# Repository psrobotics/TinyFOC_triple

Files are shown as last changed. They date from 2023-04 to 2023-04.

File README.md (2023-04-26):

# TinyFOC_triple

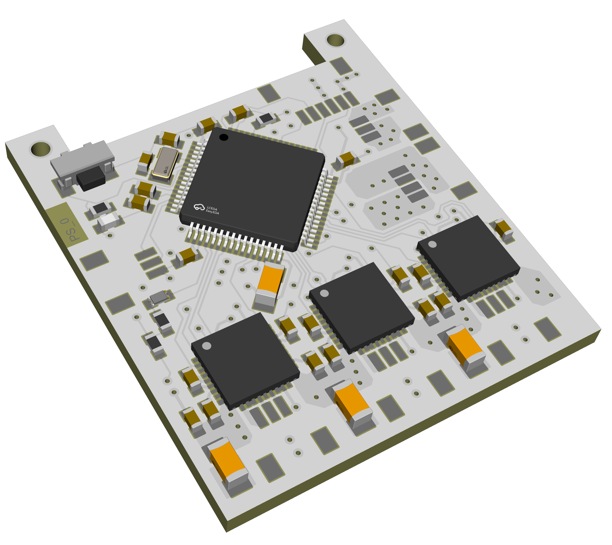
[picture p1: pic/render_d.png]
<br> <br>
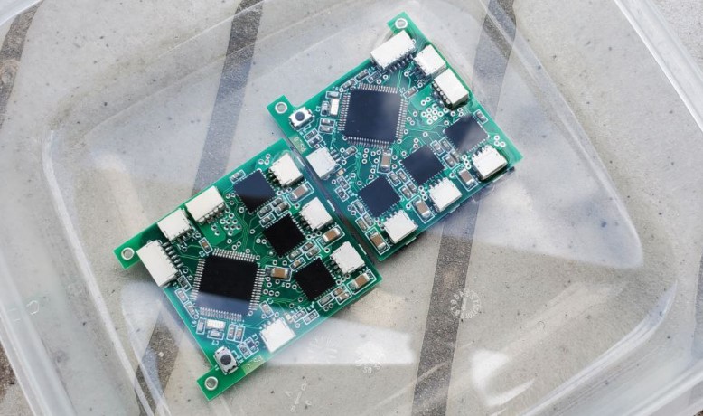
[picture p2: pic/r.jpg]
<br> <br>

* Compact 3 channel brushless motor driver with external encoder
* Supports I2C (AS5600) or AB (TLE5012B) encoders
* Hardwarer CAN, serial, SPI interface
* Input voltage: 9v - 24v, maximum phase current 1.5A
* 4 layer board / FR4 / 1.0mm thickness
* [SimpleFOC](https://github.com/simplefoc) compatible

Design file exported with [Autodesk EAGLE](https://www.autodesk.com/products/eagle/overview?term=1-YEAR&tab=subscription)

## ICs
* MCU [STM32F446RET6](https://www.st.com/en/microcontrollers-microprocessors/stm32f446re.html)
* Motor driver [DRV8313](https://www.ti.com/product/DRV8313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) or [MS8313](https://www.lcsc.com/product-detail/Others_Hangzhou-Ruimeng-Tech-MS8313_C231942.html)
* Encoder [AS5600](https://ams.com/en/as5600) or [TLE5012B E1000](https://www.infineon.com/cms/en/product/sensor/magnetic-sensors/magnetic-position-sensors/angle-sensors/tle5012b-e1000/)

## Pin Out
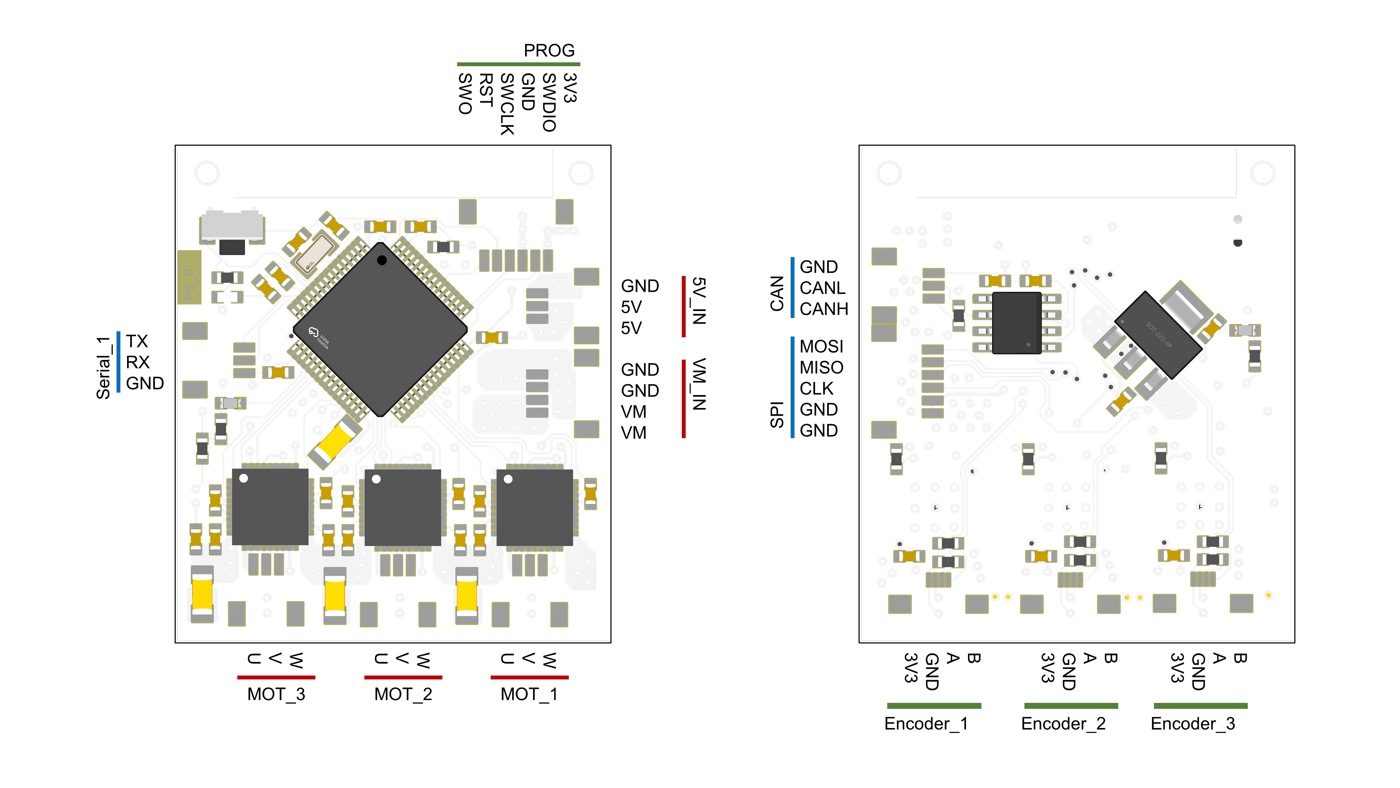
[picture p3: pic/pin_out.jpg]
<br> <br>

## License
MIT License

## Contact
* Shuang Peng, {shuangpe}@usc.edu

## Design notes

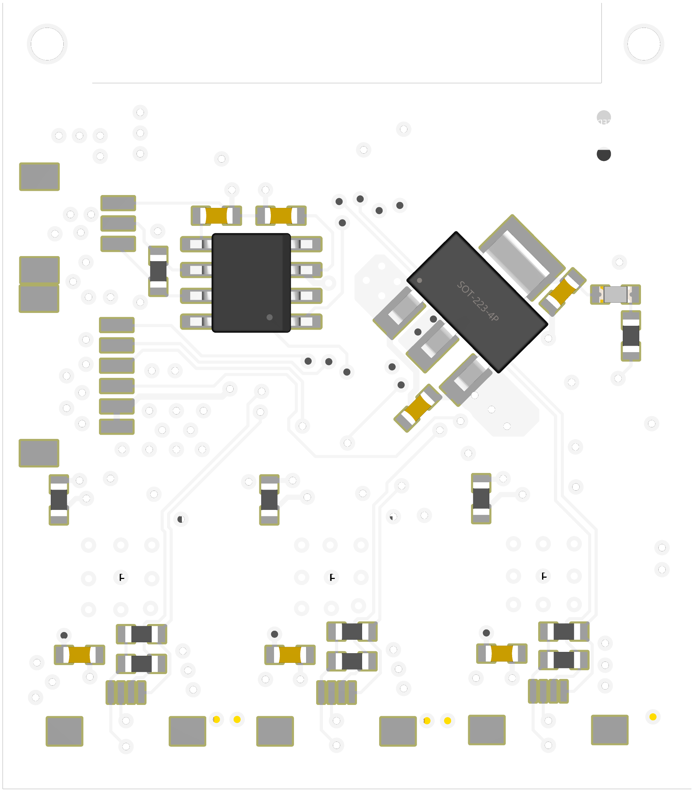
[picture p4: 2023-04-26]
pic/render_b.png

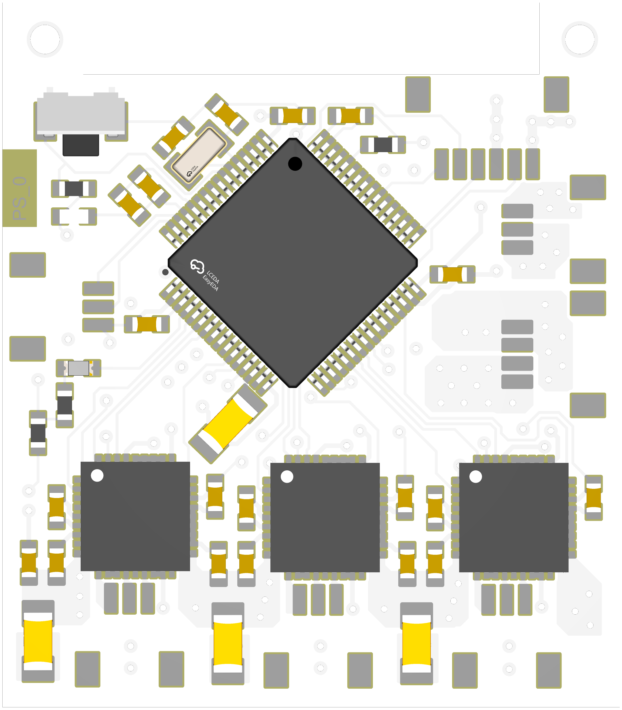
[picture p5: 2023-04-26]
pic/render_t.png

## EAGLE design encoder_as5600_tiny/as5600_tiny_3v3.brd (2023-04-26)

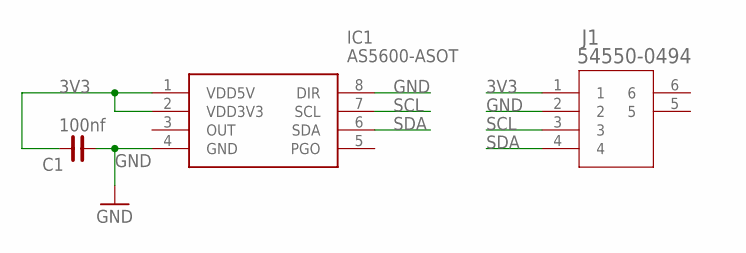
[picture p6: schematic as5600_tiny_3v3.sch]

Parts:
C1: 100nf; C0603
IC1: AS5600-ASOT; SOIC127P600X175-8N
J1: 54550-0494; CON4_1X4_DRB2_MOL

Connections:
3V3: C1.2, IC1.1 (VDD5V), IC1.2 (VDD3V3), J1.1
GND: C1.1, IC1.4 (GND), IC1.8 (DIR), J1.2
SCL: IC1.7 (SCL), J1.3
SDA: IC1.6 (SDA), J1.4

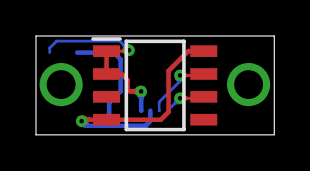
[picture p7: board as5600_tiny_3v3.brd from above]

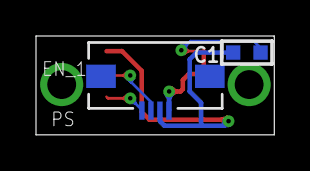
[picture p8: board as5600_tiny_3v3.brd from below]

Board: 2 copper layers, 13.2 x 5.5 mm, 3 parts (2 on the bottom side), 4 nets.

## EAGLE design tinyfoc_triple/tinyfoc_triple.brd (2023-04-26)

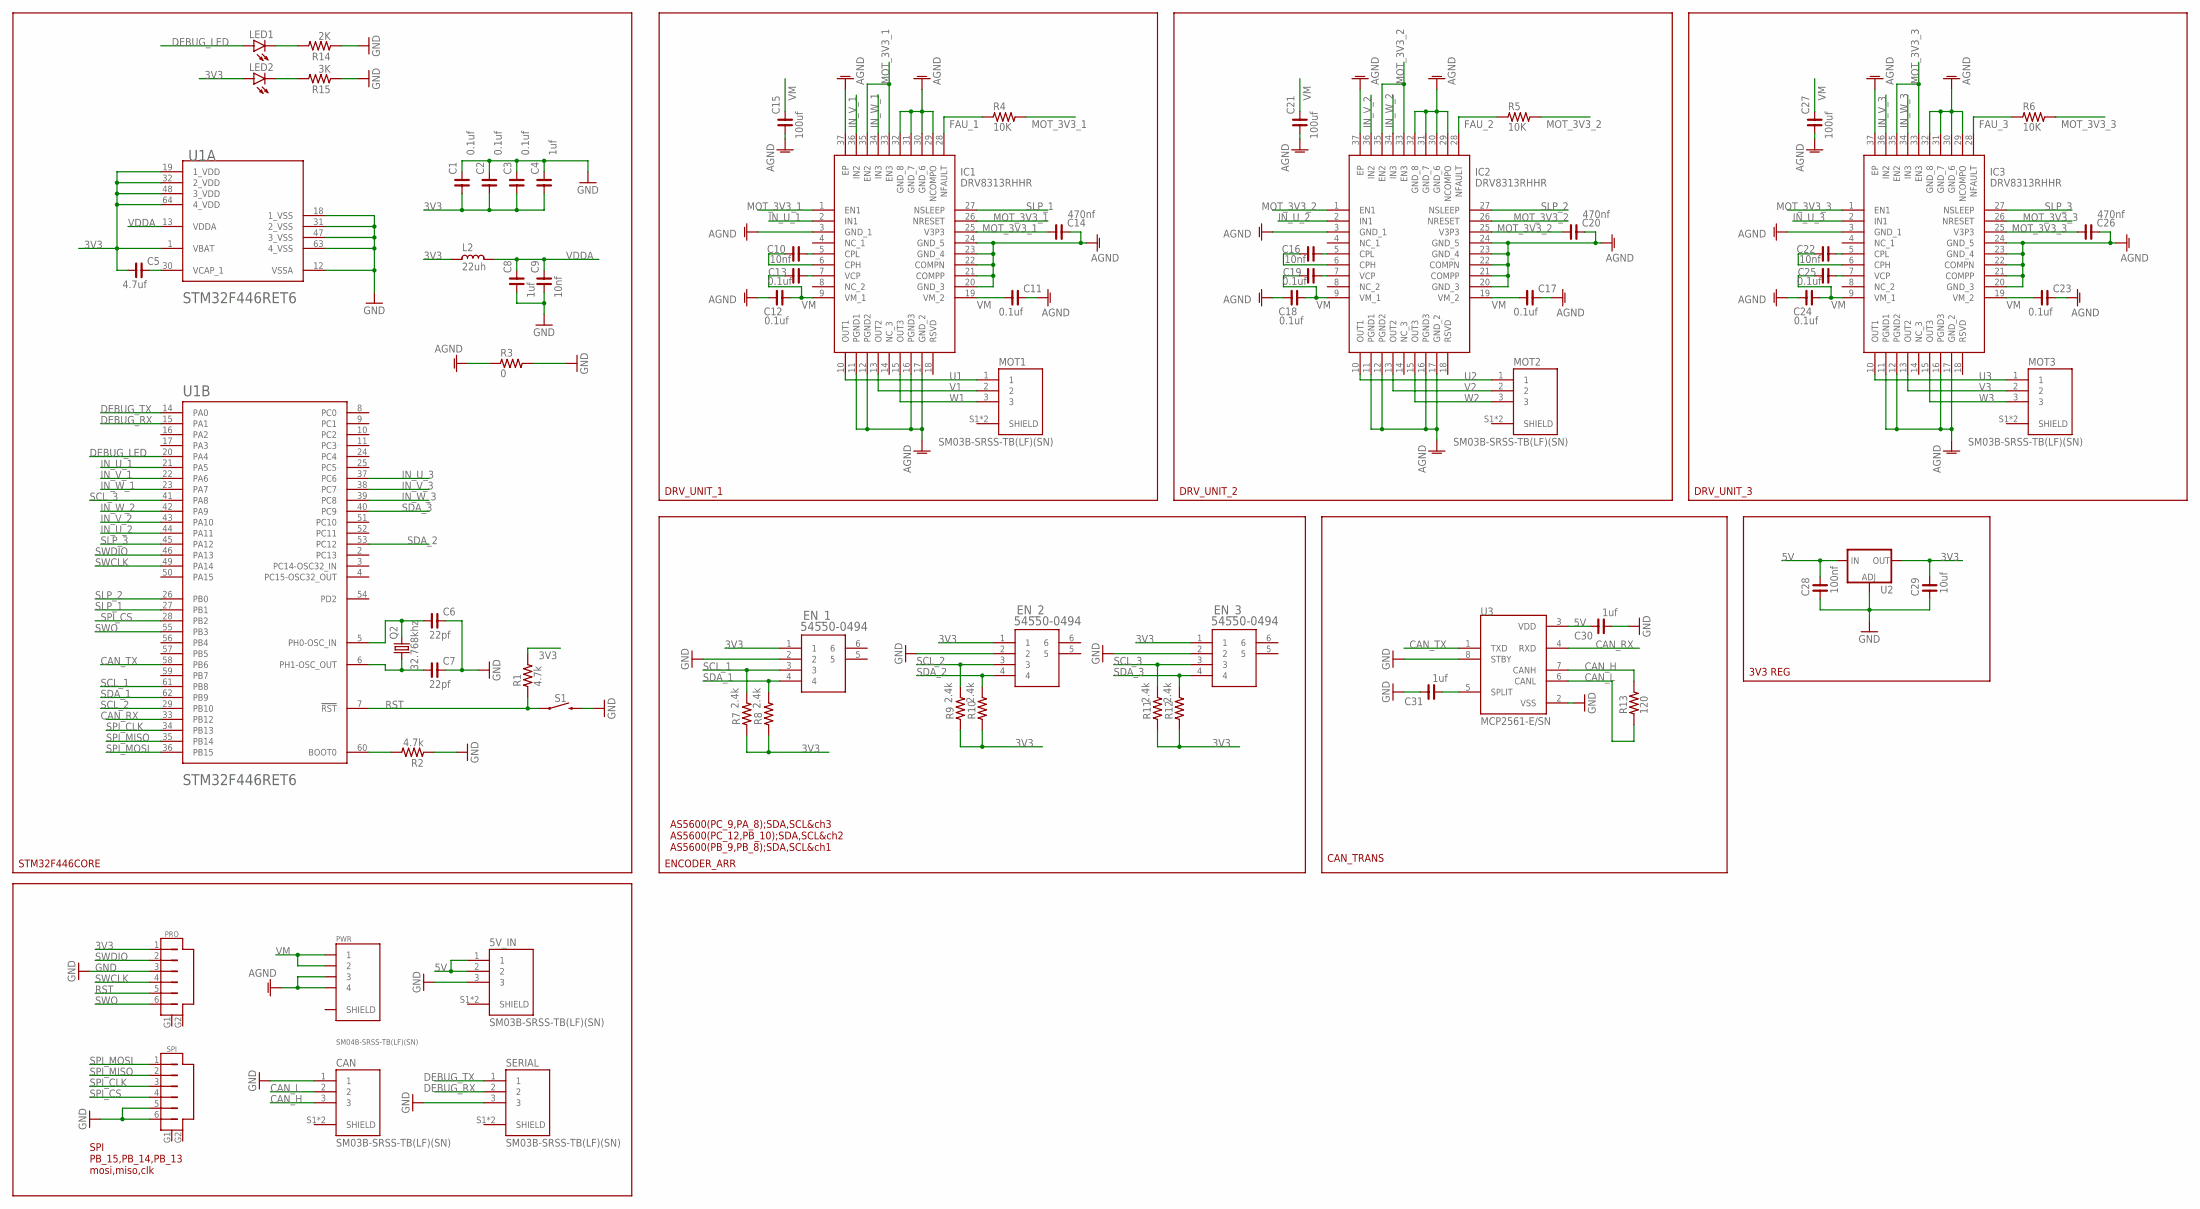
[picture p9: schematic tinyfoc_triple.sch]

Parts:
5V_IN: SM03B-SRSS-TB(LF)(SN); JST_SM03B-SRSS-TB(LF)(SN)
C1, C2, C3, C11, C12, C13, C17, C18, C19, C23, C24, C25: 0.1uf; C0603
C4, C8, C30, C31: 1uf; C0603
C5: 4.7uf; C1206
C6, C7: 22pf; C0603
C9, C10, C16, C22: 10nf; C0603
C14, C20, C26: 470nf; C0603
C15, C21, C27: 100uf; C1206
C28: 100nf; C0603
C29: 10uf; C0603
CAN: SM03B-SRSS-TB(LF)(SN); JST_SM03B-SRSS-TB(LF)(SN)
EN_1, EN_2, EN_3: 54550-0494; CON4_1X4_DRB2_MOL
IC1, IC2, IC3: DRV8313RHHR; QFN50P600X600X100-37N
L2: 22uh; PM0603
LED1, LED2: LEDCHIPLED_0603; CHIPLED_0603
MOT1, MOT2, MOT3: SM03B-SRSS-TB(LF)(SN); JST_SM03B-SRSS-TB(LF)(SN)
PRO: SM06B-SRSS-TB; SM06B
PWR: SM04B-SRSS-TB(LF)(SN); JST_SM04B-SRSS-TB(LF)(SN)
Q2: 32.768khz; 3.2X1.5
R1, R2: 4.7k; R0603
R3: 0; R0603
R4, R5, R6: 10K; R0603
R7, R8, R9, R10, R11, R12: 2.4k; R0603
R13: 120; R0603
R14: 2K; R0603
R15: 3K; R0603
S1: MOMENTARY-SWITCH-SPST-SMD-RIGHT-ANGLE; TACTILE_SWITCH_SMD_RIGHT_ANGLE
SERIAL: SM03B-SRSS-TB(LF)(SN); JST_SM03B-SRSS-TB(LF)(SN)
SPI: SM06B-SRSS-TB; SM06B
U1: STMICROELECTRONICS_STM32F446RET6STMICROELECTRONIC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; STMICROELECTRONICS_STM32F446RET6_0
U2: V_REG_LM1117SOT223; SOT223
U3: MCP2561-E/SN; SOIC127P600X175-8N

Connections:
3V3: C1.1, C2.1, C3.1, C4.1, C5.1, C29.2, EN_1.1, EN_2.1, EN_3.1, L2.2, LED2.A, PRO.1, R1.2, R7.1, R8.1, R9.1, R10.1, R11.1, R12.1, U1.1 (VBAT), U1.19 (1_VDD), U1.32 (2_VDD), U1.48 (3_VDD), U1.64 (4_VDD), U2.2 (OUT), U2.4 (OUT)
5V: 5V_IN.1, 5V_IN.2, C28.2, C30.2, U2.3 (IN), U3.3 (VDD)
AGND: C11.2, C12.1, C14.2, C15.1, C17.2, C18.1, C20.2, C21.1, C23.2, C24.1, C26.2, C27.1, IC1.3 (GND_1), IC1.11 (PGND1), IC1.12 (PGND2), IC1.16 (PGND3), IC1.17 (GND_2), IC1.20 (GND_3), IC1.21 (COMPP), IC1.22 (COMPN), IC1.23 (GND_4), IC1.24 (GND_5), IC1.29 (NCOMPO), IC1.30 (GND_6), IC1.31 (GND_7), IC1.32 (GND_8), IC1.37 (EP), IC2.3 (GND_1), IC2.11 (PGND1), IC2.12 (PGND2), IC2.16 (PGND3), IC2.17 (GND_2), IC2.20 (GND_3), IC2.21 (COMPP), IC2.22 (COMPN), IC2.23 (GND_4), IC2.24 (GND_5), IC2.29 (NCOMPO), IC2.30 (GND_6), IC2.31 (GND_7), IC2.32 (GND_8), IC2.37 (EP), IC3.3 (GND_1), IC3.11 (PGND1), IC3.12 (PGND2), IC3.16 (PGND3), IC3.17 (GND_2), IC3.20 (GND_3), IC3.21 (COMPP), IC3.22 (COMPN), IC3.23 (GND_4), IC3.24 (GND_5), IC3.29 (NCOMPO), IC3.30 (GND_6), IC3.31 (GND_7), IC3.32 (GND_8), IC3.37 (EP), PWR.3, PWR.4, R3.1
CAN_H: CAN.3, R13.2, U3.7 (CANH)
CAN_L: CAN.2, R13.1, U3.6 (CANL)
CAN_RX: U1.33 (PB12), U3.4 (RXD)
CAN_TX: U1.58 (PB6), U3.1 (TXD)
DEBUG_LED: LED1.A, U1.20 (PA4)
DEBUG_RX: SERIAL.2, U1.15 (PA1)
DEBUG_TX: SERIAL.1, U1.14 (PA0)
FAU_1: IC1.28 (NFAULT), R4.1
FAU_2: IC2.28 (NFAULT), R5.1
FAU_3: IC3.28 (NFAULT), R6.1
GND: 5V_IN.3, C1.2, C2.2, C3.2, C4.2, C6.2, C7.2, C8.1, C9.1, C28.1, C29.1, C30.1, C31.2, CAN.1, EN_1.2, EN_2.2, EN_3.2, PRO.3, R2.1, R3.2, R14.1, R15.1, S1.2, SERIAL.3, SPI.5, SPI.6, U1.12 (VSSA), U1.18 (1_VSS), U1.31 (2_VSS), U1.47 (3_VSS), U1.63 (4_VSS), U2.1 (ADJ), U3.2 (VSS), U3.8 (STBY)
IN_U_1: IC1.2 (IN1), U1.21 (PA5)
IN_U_2: IC2.2 (IN1), U1.44 (PA11)
IN_U_3: IC3.2 (IN1), U1.37 (PC6)
IN_V_1: IC1.36 (IN2), U1.22 (PA6)
IN_V_2: IC2.36 (IN2), U1.43 (PA10)
IN_V_3: IC3.36 (IN2), U1.38 (PC7)
IN_W_1: IC1.34 (IN3), U1.23 (PA7)
IN_W_2: IC2.34 (IN3), U1.42 (PA9)
IN_W_3: IC3.34 (IN3), U1.39 (PC8)
MOT_3V3_1: C14.1, IC1.1 (EN1), IC1.25 (V3P3), IC1.26 (NRESET), IC1.33 (EN3), IC1.35 (EN2), R4.2
MOT_3V3_2: C20.1, IC2.1 (EN1), IC2.25 (V3P3), IC2.26 (NRESET), IC2.33 (EN3), IC2.35 (EN2), R5.2
MOT_3V3_3: C26.1, IC3.1 (EN1), IC3.25 (V3P3), IC3.26 (NRESET), IC3.33 (EN3), IC3.35 (EN2), R6.2
unnamed: C5.2, U1.30 (VCAP_1)
unnamed: R2.2, U1.60 (BOOT0)
unnamed: C7.1, Q2.1, U1.6 (PH1-OSC_OUT)
unnamed: C10.2, IC1.5 (CPL)
unnamed: C6.1, Q2.2, U1.5 (PH0-OSC_IN)
unnamed: C10.1, IC1.6 (CPH)
unnamed: C13.2, IC1.7 (VCP)
unnamed: C16.2, IC2.5 (CPL)
unnamed: C16.1, IC2.6 (CPH)
unnamed: C19.2, IC2.7 (VCP)
unnamed: C22.2, IC3.5 (CPL)
unnamed: C22.1, IC3.6 (CPH)
unnamed: C25.2, IC3.7 (VCP)
unnamed: C31.1, U3.5 (SPLIT)
unnamed: LED2.C, R15.2
unnamed: LED1.C, R14.2
RST: PRO.5, R1.1, S1.1, U1.7 (!RST!)
SCL_1: EN_1.3, R7.2, U1.61 (PB8)
SCL_2: EN_2.3, R9.2, U1.29 (PB10)
SCL_3: EN_3.3, R11.2, U1.41 (PA8)
SDA_1: EN_1.4, R8.2, U1.62 (PB9)
SDA_2: EN_2.4, R10.2, U1.53 (PC12)
SDA_3: EN_3.4, R12.2, U1.40 (PC9)
SLP_1: IC1.27 (NSLEEP), U1.27 (PB1)
SLP_2: IC2.27 (NSLEEP), U1.26 (PB0)
SLP_3: IC3.27 (NSLEEP), U1.45 (PA12)
SPI_CLK: SPI.3, U1.34 (PB13)
SPI_CS: SPI.4, U1.28 (PB2)
SPI_MISO: SPI.2, U1.35 (PB14)
SPI_MOSI: SPI.1, U1.36 (PB15)
SWCLK: PRO.4, U1.49 (PA14)
SWDIO: PRO.2, U1.46 (PA13)
SWO: PRO.6, U1.55 (PB3)
U1: IC1.10 (OUT1), MOT1.1
U2: IC2.10 (OUT1), MOT2.1
U3: IC3.10 (OUT1), MOT3.1
V1: IC1.13 (OUT2), MOT1.2
V2: IC2.13 (OUT2), MOT2.2
V3: IC3.13 (OUT2), MOT3.2
VDDA: C8.2, C9.2, L2.1, U1.13 (VDDA)
VM: C11.1, C12.2, C13.1, C15.2, C17.1, C18.2, C19.1, C21.2, C23.1, C24.2, C25.1, C27.2, IC1.9 (VM_1), IC1.19 (VM_2), IC2.9 (VM_1), IC2.19 (VM_2), IC3.9 (VM_1), IC3.19 (VM_2), PWR.1, PWR.2
W1: IC1.15 (OUT3), MOT1.3
W2: IC2.15 (OUT3), MOT2.3
W3: IC3.15 (OUT3), MOT3.3

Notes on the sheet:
STM32F446CORE
DRV_UNIT_1
DRV_UNIT_2
DRV_UNIT_3
ENCODER_ARR
AS5600(PC_9,PA_8);SDA,SCL&ch3 AS5600(PC_12,PB_10);SDA,SCL&ch2 AS5600(PB_9,PB_8);SDA,SCL&ch1
SPI PB_15,PB_14,PB_13 mosi,miso,clk
3V3 REG
CAN_TRANS

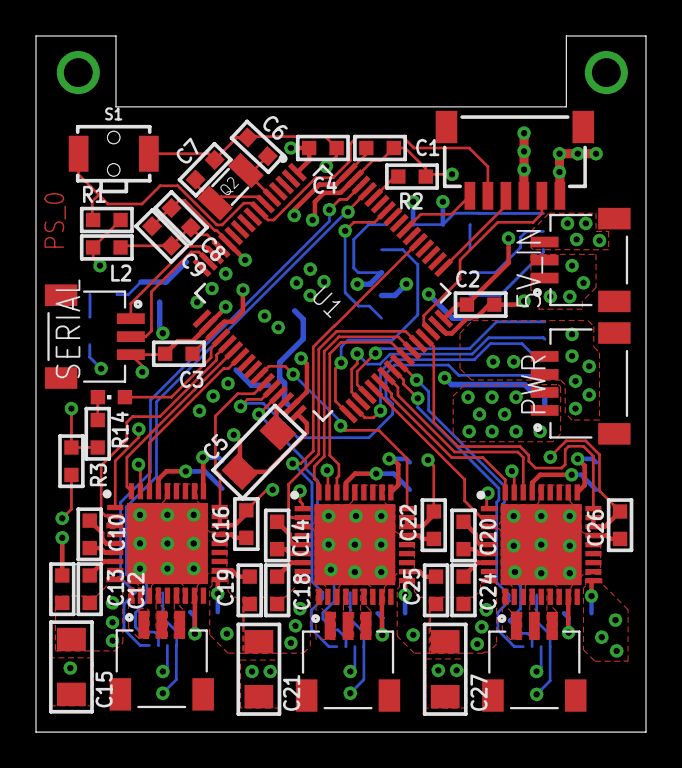
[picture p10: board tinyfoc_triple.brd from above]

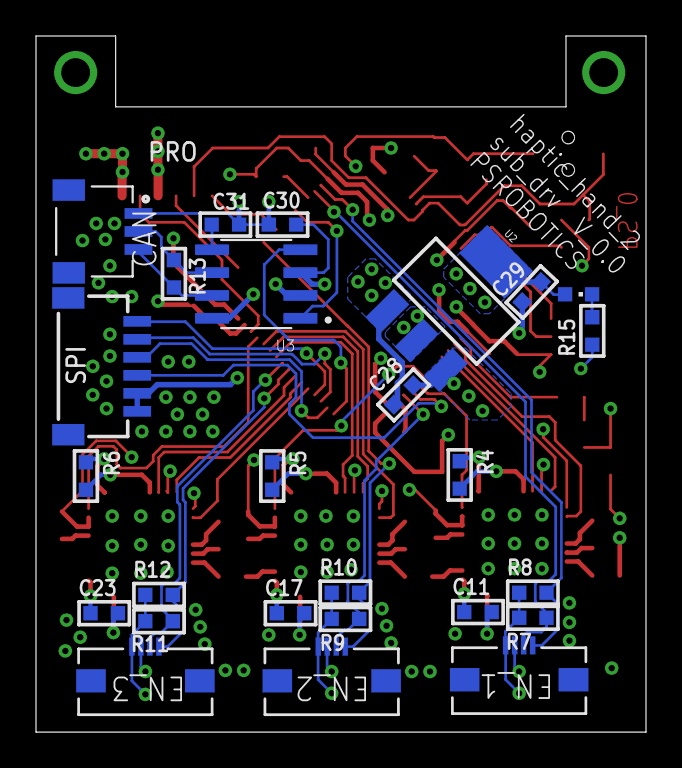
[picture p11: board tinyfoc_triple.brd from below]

Board: 4 copper layers, 33.9 x 38.7 mm, 69 parts (26 on the bottom side), 70 nets.

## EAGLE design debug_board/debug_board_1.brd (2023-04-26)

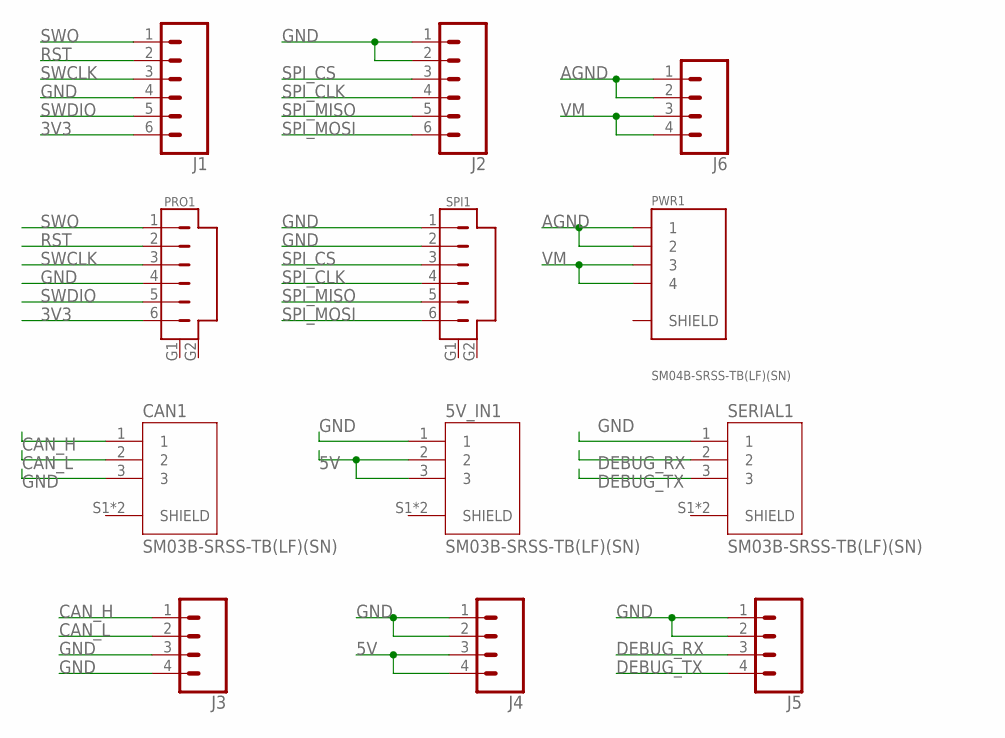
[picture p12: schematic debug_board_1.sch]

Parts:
5V_IN1: SM03B-SRSS-TB(LF)(SN); JST_SM03B-SRSS-TB(LF)(SN)
CAN1: SM03B-SRSS-TB(LF)(SN); JST_SM03B-SRSS-TB(LF)(SN)
J1, J2: CONN_06LONGPADS; 1X06_LONGPADS
J3, J4, J5, J6: CONN_04LONGPADS; 1X04_LONGPADS
PRO1: SM06B-SRSS-TB; SM06B
PWR1: SM04B-SRSS-TB(LF)(SN); JST_SM04B-SRSS-TB(LF)(SN)
SERIAL1: SM03B-SRSS-TB(LF)(SN); JST_SM03B-SRSS-TB(LF)(SN)
SPI1: SM06B-SRSS-TB; SM06B

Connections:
3V3: J1.6, PRO1.6
5V: 5V_IN1.2, 5V_IN1.3, J4.3, J4.4
AGND: J6.1, J6.2, PWR1.1, PWR1.2
CAN_H: CAN1.1, J3.1
CAN_L: CAN1.2, J3.2
DEBUG_RX: J5.3, SERIAL1.2
DEBUG_TX: J5.4, SERIAL1.3
GND: 5V_IN1.1, CAN1.3, J1.4, J2.1, J2.2, J3.3, J3.4, J4.1, J4.2, J5.1, J5.2, PRO1.4, SERIAL1.1, SPI1.1, SPI1.2
RST: J1.2, PRO1.2
SPI_CLK: J2.4, SPI1.4
SPI_CS: J2.3, SPI1.3
SPI_MISO: J2.5, SPI1.5
SPI_MOSI: J2.6, SPI1.6
SWCLK: J1.3, PRO1.3
SWDIO: J1.5, PRO1.5
SWO: J1.1, PRO1.1
VM: J6.3, J6.4, PWR1.3, PWR1.4

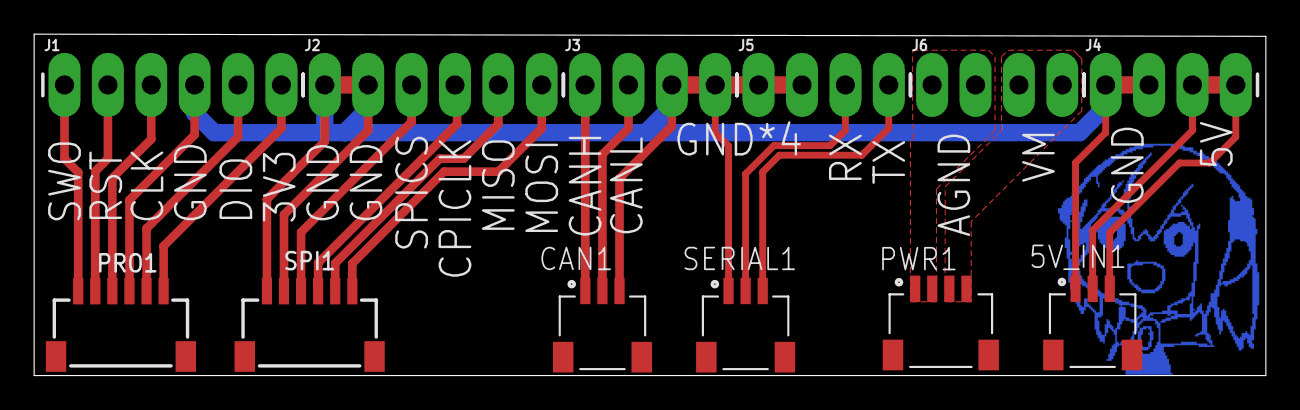
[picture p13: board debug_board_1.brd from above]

Board: 2 copper layers, 72.1 x 20.0 mm, 13 parts (0 on the bottom side), 17 nets.

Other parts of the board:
U$1: SODAYO_1

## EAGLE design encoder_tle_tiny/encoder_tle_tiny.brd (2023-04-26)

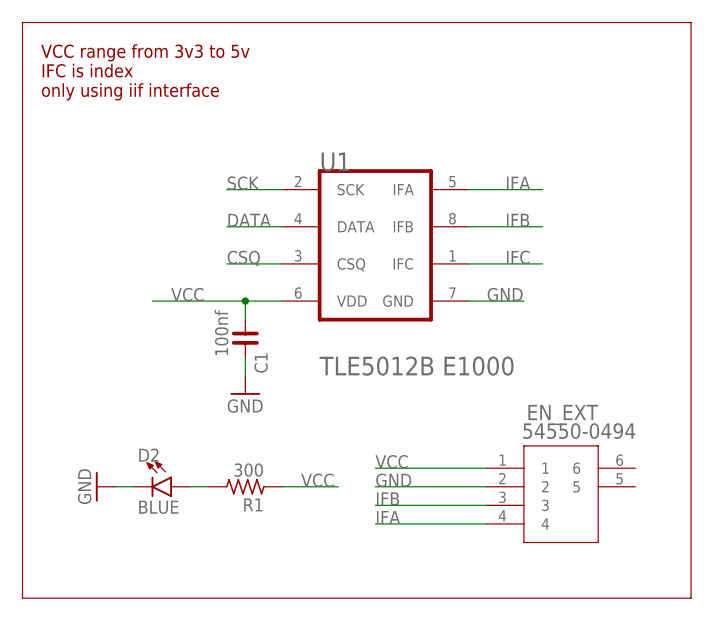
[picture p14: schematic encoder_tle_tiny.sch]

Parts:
C1: 100nf; C0603
D2: BLUE; LED-0603
EN_EXT: 54550-0494; CON4_1X4_DRB2_MOL
R1: 300; R0603
U1: INFINEON_TLE5012B_E1000INFINEON_TLE5012B_E1000_0_1; INFINEON_TLE5012B_E1000_1

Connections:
CSQ: U1.3 (CSQ)
DATA: U1.4 (DATA)
GND: C1.2, D2.C, EN_EXT.2, U1.7 (GND)
IFA: EN_EXT.4, U1.5 (IFA)
IFB: EN_EXT.3, U1.8 (IFB)
IFC: U1.1 (IFC)
unnamed: D2.A, R1.2
SCK: U1.2 (SCK)
VCC: C1.1, EN_EXT.1, R1.1, U1.6 (VDD)

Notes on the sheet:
VCC range from 3v3 to 5v IFC is index only using iif interface

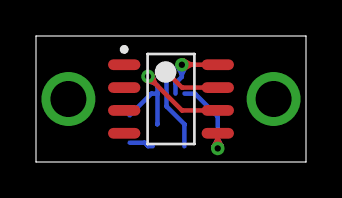
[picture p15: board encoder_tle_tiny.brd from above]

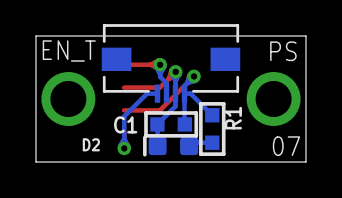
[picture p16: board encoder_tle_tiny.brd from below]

Board: 2 copper layers, 15.0 x 7.0 mm, 5 parts (4 on the bottom side), 5 nets.

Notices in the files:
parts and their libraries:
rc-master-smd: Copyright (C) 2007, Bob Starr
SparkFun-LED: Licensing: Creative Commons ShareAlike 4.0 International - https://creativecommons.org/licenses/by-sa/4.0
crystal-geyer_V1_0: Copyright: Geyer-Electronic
